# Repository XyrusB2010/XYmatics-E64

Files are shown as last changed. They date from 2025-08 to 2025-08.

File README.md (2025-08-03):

# XYmatics E64
XYmatics E64 (Engine, 64-bit) is a 5-axis Klipper mainboard, powered by a Raspberry Pi CM4 and STM32F407. It was originally built for <a href='https://github.com/XyrusB2010/XYmatics-Alpha/tree/main'>XYmatics Alpha</a>, but you can also use it for most 3D Printers.

## E64 Features
- Powered by STM32F407VET6 (MCU) and Raspberry Pi CM4 (Host)
- 1 USB-micro OTG port + 2 USB-A ports + 1 USB JST breakout, 100 Mbit RJ45 Socket for LAN, Micro SD card for extra storage
- 5 TMC2209 Stepsticks to drive stepper motors
- 3 Endstops/Switches
- 5 Controllable fans on base board + 1 for Raspberry Pi
- 8 CAN FD bus ports to reduce amount of cables
- CSI for camera input
- HDMI or DSI for display output
- I2C bus broken out

## E64 PCB
E64 PCB

# XYmatics X42
XYmatics X42 (Xpansion, for 42mm motors) is a Klipper expansion board, designed to mount onto 42mm stepper motors. Powered by a STM32G0B1, it communicates to the E64 mainboard through CAN FD. This board simplifies the mainboard, and reduces the amount of cables going out. The X42 can also be used with most other 3D Printers.

## X42 Features
- Powered by STM32G0B1CBT6
- Supports Laser engravers, CNC routers and FDM extruders
- TJA1051T CAN FD module to communicate with E64
- ~~BLTouch compatible~~
- Two PWM controllable fans
- ADXL345 accelerometer included
- ~~3~~ 1 Endstop/Switch
- I2C bus ~~and neopixel~~ broken out
>  [!NOTE]
>  May re-add these removed features in future if possible.

## X42 PCB
X42 PCB front view
X42 PCB back view

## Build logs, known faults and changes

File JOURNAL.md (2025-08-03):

---
title: "XYmatics-E64"
author: "Xyrus Babao"
description: "5-axis Klipper-powered mainboard"
created_at: "2025-07-07"
---

### <b>Total time spent: 13 hours 45 minutes</b>

# 7/07/2025 - Begin PCB design
For the PCB design, I am using KiCad with a few components imported from <a href="https://snapeda.com/">SnapEDA.</a> I have named <a href='https://github.com/XyrusB2010/XYmatics-Alpha/tree/main'>XYmatics-Alpha's</a> mainboard E64 (Engine64). It utilises a CM4/CM5 compute module running Klipper firmware to control the main MCU - an STM32F407. Like most Klipper systems, the compute module does not directly control the motors, sensors, etc, and instead outputs commands via USB to the STM32. I have completed desigining the Compute module side, and just need to complete the STM32 and other components. Below is an image of the CM4 schematic.

XYmatics-E64 CM4 schematic

(Excuse the resolution, you can view a PDF of the schematic <a href="https://github.com/XyrusB2010/XYmatics-E64/blob/main/Schematics/xymatics-e64.pdf">here.</a>)

<b>Total time - 45 minutes</b>

# 14/07/2025 - Finish STM32 schematic and begin X42 schematic
Today I have completed the schematic for the STM32F407. It has what most other 3D Printer mainboards have, but also includes 8 CAN FD bus ports for connecting expansion boards (XYmatics-X42). It uses the high-speed TJA1051T for CAN FD communication. 5 TMC2209 Stepsticks are used to drive the main stepper motors. 5 controllable fans are included, as well as another MOSFET for the heatbed. 3 endstops/switches are included to home the printer. The entire system runs on 24V, which is the standard for most 3D printer mainboards.

XYmatics-E64 STM32F407 schematic

<a href="https://github.com/XyrusB2010/XYmatics-E64/blob/main/Schematics/xymatics-e64.pdf">Link to schematic PDF</a>

<b>Total time - 2 hours 15 minutes</b>

# 20/07/2025 - Finish X42 schematic
I have now finished the schematic for the X42. It is quite similar to the BIGTREETECH EBB42 and Mellow Fly SHT-42, but also contains a MOSFET to drive a laser engraver or router motor. Unfortunately, I haven't broken out a USB port yet (although I may fix this in the future). This means the only other way to flash Klipper is through an ST-LINK, or other JTAG/SWD programmer. You can obtain these through Aliexpress for <$2 USD. The X42 also doesn't use a Stepstick driver like the E64 mainboard, but has a directly soldered TMC2209 instead. After looking through the schematics one more time, I should be ready to start designing the PCBs.

XYmatics-E64 X42 schematic

<b>Total time - 2 hours</b>

# 23/07/2025 - Update on X42
The X42 PCB is about 75% completed, I just need to route the components for the CNC router/laser. Due to the limited amount of space on the PCB, some of the components are mounted on the back side (currently just the power supply and regulators). So far the CAN BUS, SWD, Stepper motor, Thermistor, Hotend, Fans, I2C Bus and Buttons have been placed and routed. Unfortunately, I have temporarily removed the Neopixel and BLTouch breakouts due to the lack of space, although I may re-add them later on. Below is an unfinished 3D render of the X42 PCB:

X42 PCB front view
X42 PCB back view

<b>Total time - 1 hour 45 minutes</b>

# 25/07/2025 - Finish X42 PCB
I have now finished designing the PCB for the X42. All GPIOs/breakouts are on the front side, while the power supply and ADXL345 are mounted on the back. Endstops have also been removed due to the small amount of remaining space. This will be added in the first revision. I will begin to route the Raspberry Pi components on the E64, starting with the power supply. Below is a completed 3D render of the X42 PCB:

X42 PCB front view
X42 PCB back view

<b>Total time - 2 hours</b>

# 31/07/2025 - E64 PCB complete
6 days later, the E64 PCB has been finished. Please note that the RPI-GPIO isn't fully broken out, only +5V, +3.3V and I2C Bus have been. Notice how the RPI electronics are on one side while the F407 is on the other, this is to reduce complications with the design. 3 M3 mounting holes have been placed in the corners. The rough dimensions of the board are 192x98mm. The next step is to write the firmware for Klipper, which shouldn't be too hard. Here is a 3D render of the E64 PCB:

E64 PCB front view

<b>Total time - 3 hours</b>

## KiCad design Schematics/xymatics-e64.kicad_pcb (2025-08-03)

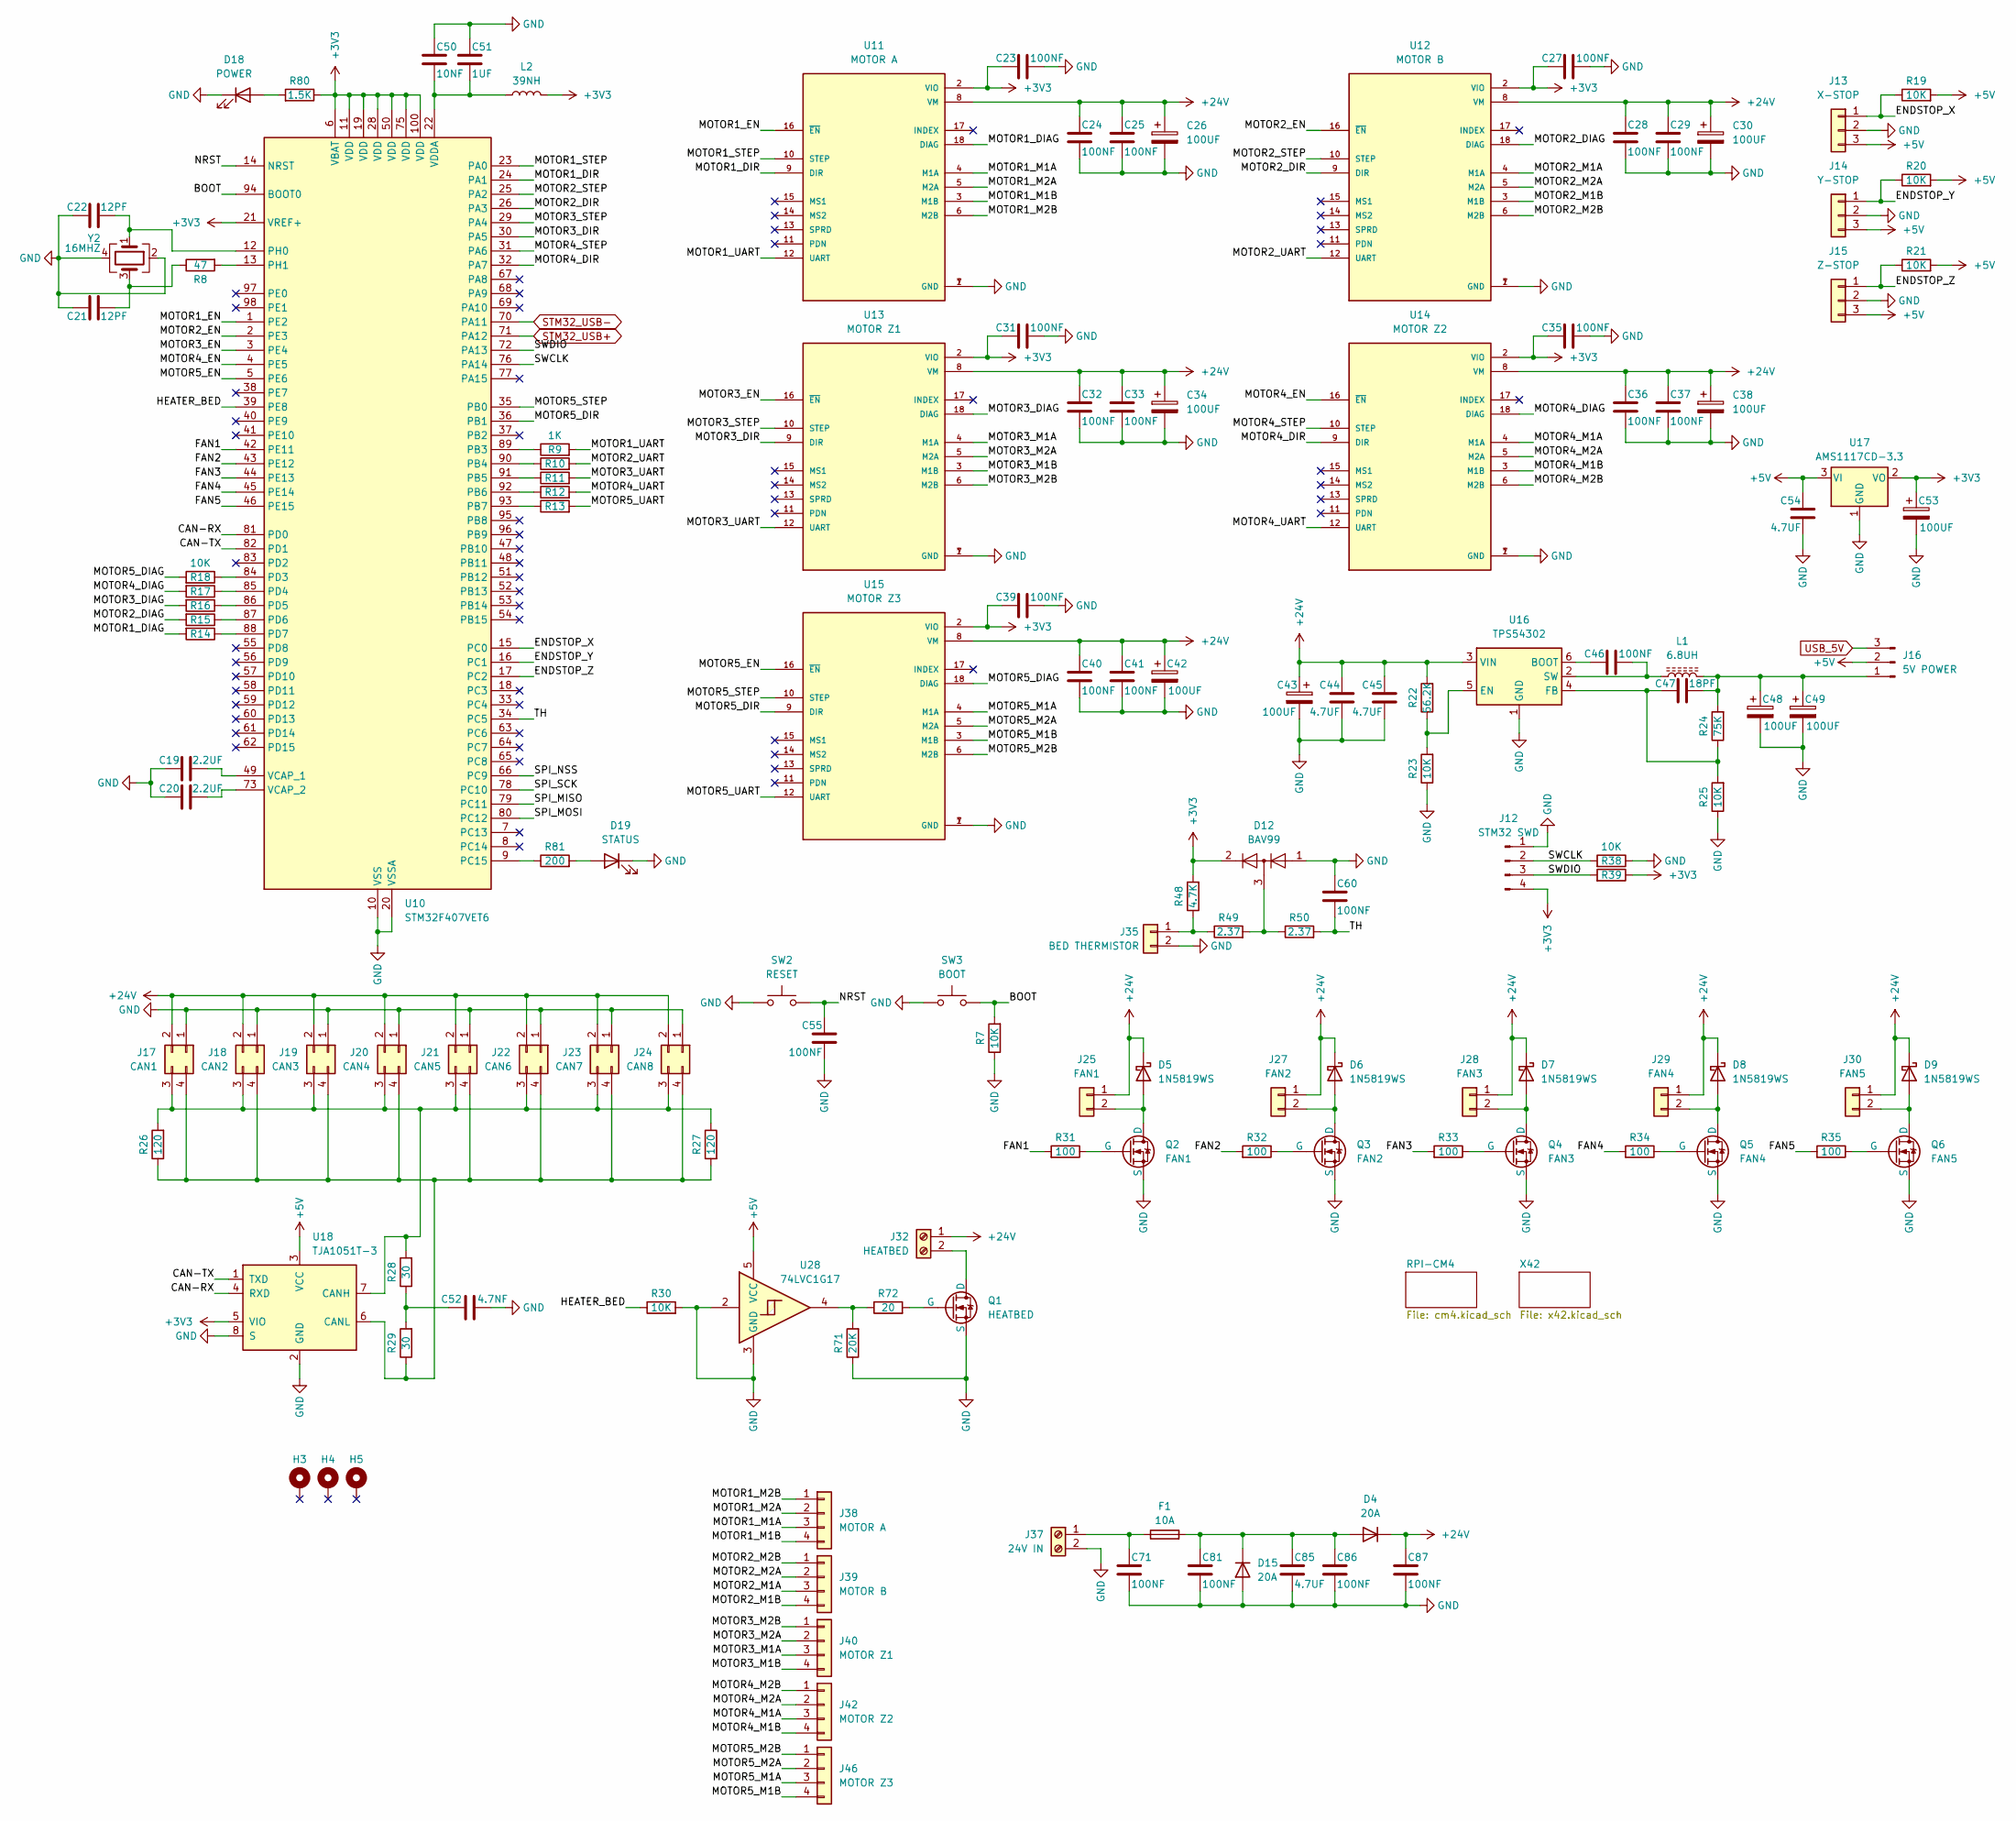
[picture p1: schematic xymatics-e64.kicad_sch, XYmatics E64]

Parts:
C19, C20: 2.2UF; C_0805_2012Metric
C21, C22: 12PF; C_0805_2012Metric
C23, C24, C25, C27, C28, C29, C31, C32, C33, C35, C36, C37, C39, C40, C41, C46, C55, C60, C71, C81, C86, C87: 100NF; C_0805_2012Metric
C26, C30, C34, C38, C42, C43, C48, C49, C53: 100UF; CP_Elec_5x3
C44, C45, C54, C85: 4.7UF; C_0805_2012Metric
C47: 18PF; C_0805_2012Metric
C50: 10NF; C_0805_2012Metric
C51: 1UF; C_0805_2012Metric
C52: 4.7NF; C_0805_2012Metric
D4, D15: 20A; D_SMB
D5, D6, D7, D8, D9: 1N5819WS; D_SOD-323
D12: BAV99; SOT-23
D18: POWER; LED_0805_2012Metric
D19: STATUS; LED_0805_2012Metric
F1: 10A; Fuse_Blade_ATO_directSolder
H3, H4, H5: MountingHole_Pad; MountingHole_3mm_Pad
J12: STM32 SWD; PinHeader_1x04_P2.54mm_Vertical
J13: X-STOP; JST_XH_B3B-XH-A_1x03_P2.50mm_Vertical
J14: Y-STOP; JST_XH_B3B-XH-A_1x03_P2.50mm_Vertical
J15: Z-STOP; JST_XH_B3B-XH-A_1x03_P2.50mm_Vertical
J16: 5V POWER; PinHeader_1x03_P2.54mm_Vertical
J17: CAN1; Molex_Micro-Fit_3.0_43045-0412_2x02_P3.00mm_Vertical
J18: CAN2; Molex_Micro-Fit_3.0_43045-0412_2x02_P3.00mm_Vertical
J19: CAN3; Molex_Micro-Fit_3.0_43045-0412_2x02_P3.00mm_Vertical
J20: CAN4; Molex_Micro-Fit_3.0_43045-0412_2x02_P3.00mm_Vertical
J21: CAN5; Molex_Micro-Fit_3.0_43045-0412_2x02_P3.00mm_Vertical
J22: CAN6; Molex_Micro-Fit_3.0_43045-0412_2x02_P3.00mm_Vertical
J23: CAN7; Molex_Micro-Fit_3.0_43045-0412_2x02_P3.00mm_Vertical
J24: CAN8; Molex_Micro-Fit_3.0_43045-0412_2x02_P3.00mm_Vertical
J25: FAN1; JST_XH_B2B-XH-A_1x02_P2.50mm_Vertical
J27: FAN2; JST_XH_B2B-XH-A_1x02_P2.50mm_Vertical
J28: FAN3; JST_XH_B2B-XH-A_1x02_P2.50mm_Vertical
J29: FAN4; JST_XH_B2B-XH-A_1x02_P2.50mm_Vertical
J30: FAN5; JST_XH_B2B-XH-A_1x02_P2.50mm_Vertical
J32: HEATBED; TerminalBlock_MaiXu_MX126-5.0-02P_1x02_P5.00mm
J35: BED THERMISTOR; JST_XH_B2B-XH-A_1x02_P2.50mm_Vertical
J37: 24V IN; TerminalBlock_MaiXu_MX126-5.0-02P_1x02_P5.00mm
J38: MOTOR A; JST_XH_B4B-XH-A_1x04_P2.50mm_Vertical
J39: MOTOR B; JST_XH_B4B-XH-A_1x04_P2.50mm_Vertical
J40: MOTOR Z1; JST_XH_B4B-XH-A_1x04_P2.50mm_Vertical
J42: MOTOR Z2; JST_XH_B4B-XH-A_1x04_P2.50mm_Vertical
J46: MOTOR Z3; JST_XH_B4B-XH-A_1x04_P2.50mm_Vertical
L1: 6.8UH; L_6.3x6.3_H3
L2: 39NH; L_0805_2012Metric
Q1: HEATBED; TO-252-2
Q2: FAN1; SOT-23
Q3: FAN2; SOT-23
Q4: FAN3; SOT-23
Q5: FAN4; SOT-23
Q6: FAN5; SOT-23
R7, R14, R15, R16, R17, R18, R19, R20, R21, R23, R25, R30, R38, R39: 10K; R_0805_2012Metric
R8: 47; R_0805_2012Metric
R9, R10, R11, R12, R13: 1K; R_0805_2012Metric
R22: 56.2K; R_1206_3216Metric
R24: 75K; R_1206_3216Metric
R26, R27: 120; R_0805_2012Metric
R28, R29: 30; R_0805_2012Metric
R31, R32, R33, R34, R35: 100; R_0805_2012Metric
R48: 4.7K; R_0805_2012Metric
R49, R50: 2.37; R_0805_2012Metric
R71: 20K; R_0805_2012Metric
R72: 20; R_0805_2012Metric
R80: 1.5K; R_0805_2012Metric
R81: 200; R_0805_2012Metric
SW2: RESET; SW_Tactile_SPST_NO_Straight_CK_PTS636Sx25SMTRLFS
SW3: BOOT; SW_Tactile_SPST_NO_Straight_CK_PTS636Sx25SMTRLFS
U10: STM32F407VET6; LQFP-100_14x14mm_P0.5mm
U11: MOTOR A; MODULE_TMC2209_SILENTSTEPSTICK; PARTREV 1.20
U12: MOTOR B; MODULE_TMC2209_SILENTSTEPSTICK; PARTREV 1.20
U13: MOTOR Z1; MODULE_TMC2209_SILENTSTEPSTICK; PARTREV 1.20
U14: MOTOR Z2; MODULE_TMC2209_SILENTSTEPSTICK; PARTREV 1.20
U15: MOTOR Z3; MODULE_TMC2209_SILENTSTEPSTICK; PARTREV 1.20
U16: TPS54302; SOT-23-6
U17: AMS1117CD-3.3; TO-252-2
U18: TJA1051T-3; SOIC-8_3.9x4.9mm_P1.27mm
U28: 74LVC1G17; SOT-23-5
Y2: 16MHZ; Crystal_SMD_Abracon_ABM3B-4Pin_5.0x3.2mm

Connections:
+3V3: C23.2, C27.2, C31.2, C35.2, C39.2, C53.1, D12.2 (A), J12.4, L2.2, R39.1, R48.2, R80.1, U10.6 (VBAT), U10.11 (VDD), U10.19 (VDD), U10.21 (VREF+), U10.28 (VDD), U10.50 (VDD), U10.75 (VDD), U10.100 (VDD), U11.2 (VIO), U12.2 (VIO), U13.2 (VIO), U14.2 (VIO), U15.2 (VIO), U17.2 (VO), U18.5 (VIO)
+5V: C54.1, J13.3, J14.3, J15.3, J16.2, R19.2, R20.2, R21.2, U17.3 (VI), U18.3 (VCC), U28.5 (VCC); also elsewhere on the board
+24V: C24.1, C25.1, C26.1, C28.1, C29.1, C30.1, C32.1, C33.1, C34.1, C36.1, C37.1, C38.1, C40.1, C41.1, C42.1, C43.1, C44.1, C45.1, C87.1, D4.1 (K), D5.1 (K), D6.1 (K), D7.1 (K), D8.1 (K), D9.1 (K), J17.2, J18.2, J19.2, J20.2, J21.2, J22.2, J23.2, J24.2, J25.1, J27.1, J28.1, J29.1, J30.1, J32.1, R22.2, U11.8 (VM), U12.8 (VM), U13.8 (VM), U14.8 (VM), U15.8 (VM), U16.3 (VIN)
/BOOT: R7.2, SW3.2, U10.94 (BOOT0)
/CAN-RX: U10.81 (PD0), U18.4 (RXD)
/CAN-TX: U10.82 (PD1), U18.1 (TXD)
/ENDSTOP_X: J13.1, R19.1, U10.15 (PC0)
/ENDSTOP_Y: J14.1, R20.1, U10.16 (PC1)
/ENDSTOP_Z: J15.1, R21.1, U10.17 (PC2)
/FAN1: R31.2, U10.42 (PE11)
/FAN2: R32.2, U10.43 (PE12)
/FAN3: R33.2, U10.44 (PE13)
/FAN4: R34.2, U10.45 (PE14)
/FAN5: R35.2, U10.46 (PE15)
/HEATER_BED: R30.1, U10.39 (PE8)
/MOTOR1_DIAG: R14.2, U11.18 (DIAG)
/MOTOR1_DIR: U10.24 (PA1), U11.9 (DIR)
/MOTOR1_EN: U10.1 (PE2), U11.16 (~EN)
/MOTOR1_M1A: J38.3, U11.4 (M1A)
/MOTOR1_M1B: J38.4, U11.3 (M1B)
/MOTOR1_M2A: J38.2, U11.5 (M2A)
/MOTOR1_M2B: J38.1, U11.6 (M2B)
/MOTOR1_STEP: U10.23 (PA0), U11.10 (STEP)
/MOTOR1_UART: R9.2, U11.12 (UART)
/MOTOR2_DIAG: R15.2, U12.18 (DIAG)
/MOTOR2_DIR: U10.26 (PA3), U12.9 (DIR)
/MOTOR2_EN: U10.2 (PE3), U12.16 (~EN)
/MOTOR2_M1A: J39.3, U12.4 (M1A)
/MOTOR2_M1B: J39.4, U12.3 (M1B)
/MOTOR2_M2A: J39.2, U12.5 (M2A)
/MOTOR2_M2B: J39.1, U12.6 (M2B)
/MOTOR2_STEP: U10.25 (PA2), U12.10 (STEP)
/MOTOR2_UART: R10.2, U12.12 (UART)
/MOTOR3_DIAG: R16.2, U13.18 (DIAG)
/MOTOR3_DIR: U10.30 (PA5), U13.9 (DIR)
/MOTOR3_EN: U10.3 (PE4), U13.16 (~EN)
/MOTOR3_M1A: J40.3, U13.4 (M1A)
/MOTOR3_M1B: J40.4, U13.3 (M1B)
/MOTOR3_M2A: J40.2, U13.5 (M2A)
/MOTOR3_M2B: J40.1, U13.6 (M2B)
/MOTOR3_STEP: U10.29 (PA4), U13.10 (STEP)
/MOTOR3_UART: R11.2, U13.12 (UART)
/MOTOR4_DIAG: R17.2, U14.18 (DIAG)
/MOTOR4_DIR: U10.32 (PA7), U14.9 (DIR)
/MOTOR4_EN: U10.4 (PE5), U14.16 (~EN)
/MOTOR4_M1A: J42.3, U14.4 (M1A)
/MOTOR4_M1B: J42.4, U14.3 (M1B)
/MOTOR4_M2A: J42.2, U14.5 (M2A)
/MOTOR4_M2B: J42.1, U14.6 (M2B)
/MOTOR4_STEP: U10.31 (PA6), U14.10 (STEP)
/MOTOR4_UART: R12.2, U14.12 (UART)
/MOTOR5_DIAG: R18.2, U15.18 (DIAG)
/MOTOR5_DIR: U10.36 (PB1), U15.9 (DIR)
/MOTOR5_EN: U10.5 (PE6), U15.16 (~EN)
/MOTOR5_M1A: J46.3, U15.4 (M1A)
/MOTOR5_M1B: J46.4, U15.3 (M1B)
/MOTOR5_M2A: J46.2, U15.5 (M2A)
/MOTOR5_M2B: J46.1, U15.6 (M2B)
/MOTOR5_STEP: U10.35 (PB0), U15.10 (STEP)
/MOTOR5_UART: R13.2, U15.12 (UART)
/NRST: C55.1, SW2.2, U10.14 (NRST)
/SPI_MISO: U10.79 (PC11)
/SPI_MOSI: U10.80 (PC12)
/SPI_NSS: U10.66 (PC9)
/SPI_SCK: U10.78 (PC10)
/SWCLK: J12.2, R38.2, U10.76 (PA14)
/SWDIO: J12.3, R39.2, U10.72 (PA13)
/TH: C60.2, R50.2, U10.34 (PC5)
GND: C19.2, C20.2, C21.1, C22.1, C23.1, C24.2, C25.2, C26.2, C27.1, C28.2, C29.2, C30.2, C31.1, C32.2, C33.2, C34.2, C35.1, C36.2, C37.2, C38.2, C39.1, C40.2, C41.2, C42.2, C43.2, C44.2, C45.2, C48.2, C49.2, C50.1, C51.1, C52.2, C53.2, C54.2, C55.2, C60.1, C71.2, C81.2, C85.2, C86.2, C87.2, D12.1 (K), D15.2 (A), D18.1 (K), D19.1 (K), J12.1, J13.2, J14.2, J15.2, J17.1, J18.1, J19.1, J20.1, J21.1, J22.1, J23.1, J24.1, J35.2, J37.2, Q1.3 (S), Q2.3 (S), Q3.3 (S), Q4.3 (S), Q5.3 (S), Q6.3 (S), R7.1, R23.1, R25.1, R30.2, R38.1, R71.1, SW2.1, SW3.1, U10.10 (VSS), U10.20 (VSSA), U10.27 (VSS), U10.74 (VSS), U10.99 (VSS), U11.1 (GND), U11.7 (GND), U12.1 (GND), U12.7 (GND), U13.1 (GND), U13.7 (GND), U14.1 (GND), U14.7 (GND), U15.1 (GND), U15.7 (GND), U16.1 (GND), U17.1 (GND), U18.2 (GND), U18.8 (S), U28.2, U28.3 (GND), Y2.2, Y2.4; also elsewhere on the board
unnamed: C21.2, R8.1, Y2.3
unnamed: C52.1, R28.1, R29.2
unnamed: D5.2 (A), J25.2, Q2.1 (D)
unnamed: D6.2 (A), J27.2, Q3.1 (D)
unnamed: D7.2 (A), J28.2, Q4.1 (D)
unnamed: D8.2 (A), J29.2, Q5.1 (D)
unnamed: D9.2 (A), J30.2, Q6.1 (D)
unnamed: D12.3 (K), R49.2, R50.1
unnamed: C81.1, C85.1, C86.1, D4.2 (A), D15.1 (K), F1.2
unnamed: D18.2 (A), R80.2
unnamed: D19.2 (A), R81.2
unnamed: C47.1, C48.1, C49.1, J16.1, L1.2, R24.2
unnamed: J17.3, J18.3, J19.3, J20.3, J21.3, J22.3, J23.3, J24.3, R26.2, R27.1, R28.2, U18.7 (CANH)
unnamed: J17.4, J18.4, J19.4, J20.4, J21.4, J22.4, J23.4, J24.4, R26.1, R27.2, R29.1, U18.6 (CANL)
unnamed: J32.2, Q1.2 (D)
unnamed: J35.1, R48.1, R49.1
unnamed: C71.1, F1.1, J37.1
unnamed: Q1.1 (G), R72.2
unnamed: Q2.2 (G), R31.1
unnamed: Q3.2 (G), R32.1
unnamed: Q4.2 (G), R33.1
unnamed: Q5.2 (G), R34.1
unnamed: Q6.2 (G), R35.1
unnamed: R71.2, R72.1, U28.4
unnamed: R9.1, U10.89 (PB3)
unnamed: R10.1, U10.90 (PB4)
unnamed: R11.1, U10.91 (PB5)
unnamed: R12.1, U10.92 (PB6)
unnamed: R13.1, U10.93 (PB7)
unnamed: R81.1, U10.9 (PC15)
unnamed: R18.1, U10.84 (PD3)
unnamed: R17.1, U10.85 (PD4)
unnamed: R16.1, U10.86 (PD5)
unnamed: R15.1, U10.87 (PD6)
unnamed: R14.1, U10.88 (PD7)
unnamed: C22.2, U10.12 (PH0), Y2.1
unnamed: R8.2, U10.13 (PH1)
unnamed: C19.1, U10.49 (VCAP_1)
unnamed: C20.1, U10.73 (VCAP_2)
unnamed: C50.2, C51.2, L2.1, U10.22 (VDDA)
unnamed: C46.2, U16.6 (BOOT)
unnamed: R22.1, R23.2, U16.5 (EN)
unnamed: C47.2, R24.1, R25.2, U16.4 (FB)
unnamed: C46.1, L1.1, U16.2 (SW)
STM32_USB+: U10.71 (PA12); also elsewhere on the board
STM32_USB-: U10.70 (PA11); also elsewhere on the board
USB_5V: J16.3; also elsewhere on the board

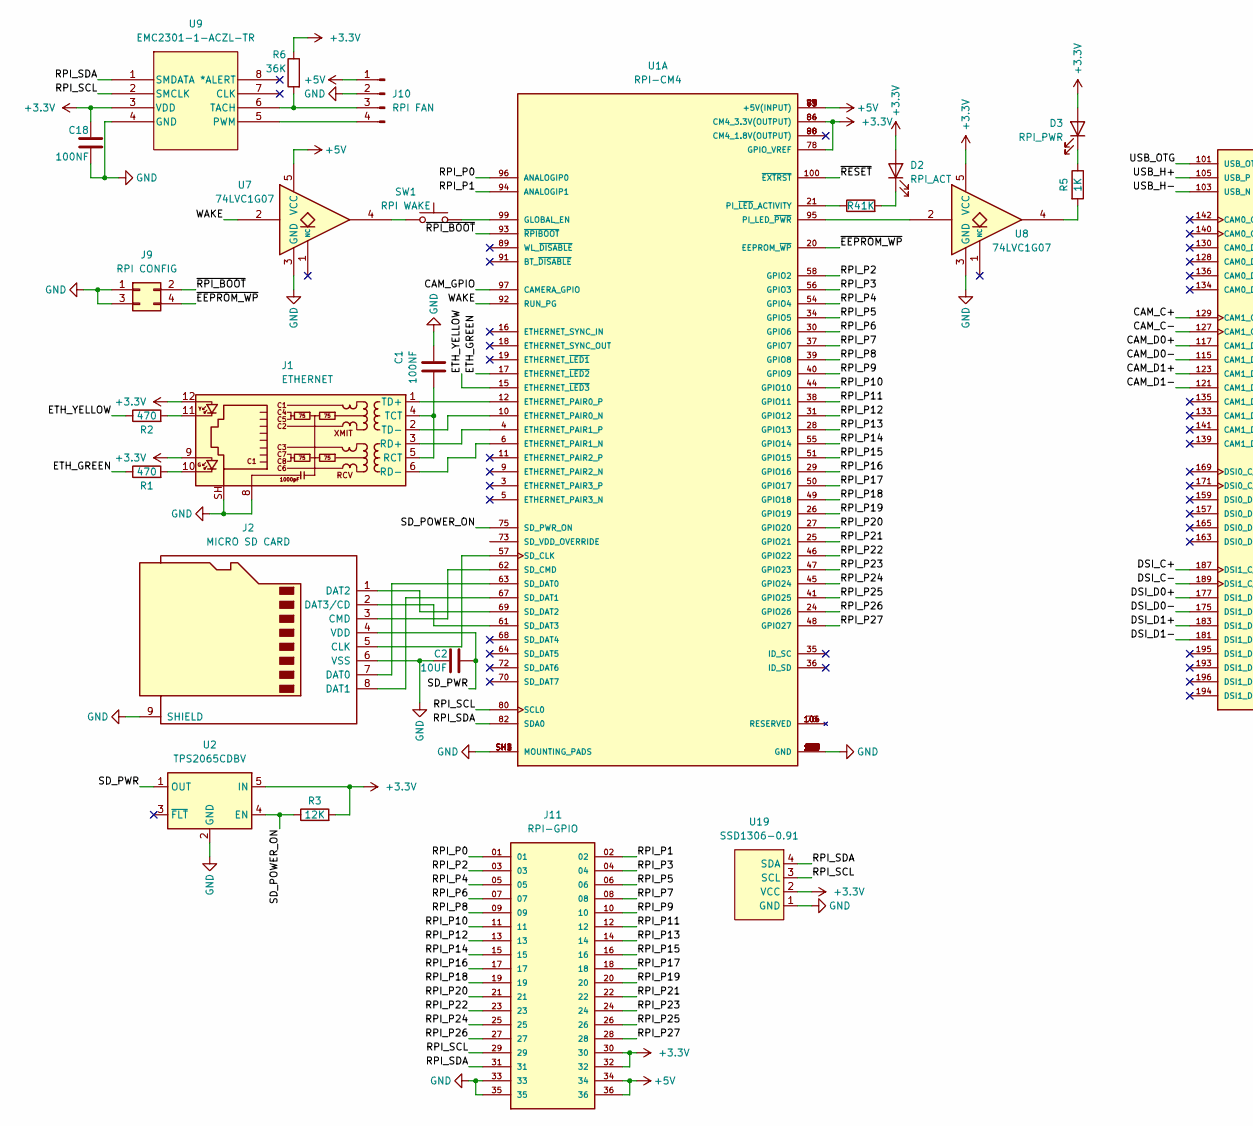
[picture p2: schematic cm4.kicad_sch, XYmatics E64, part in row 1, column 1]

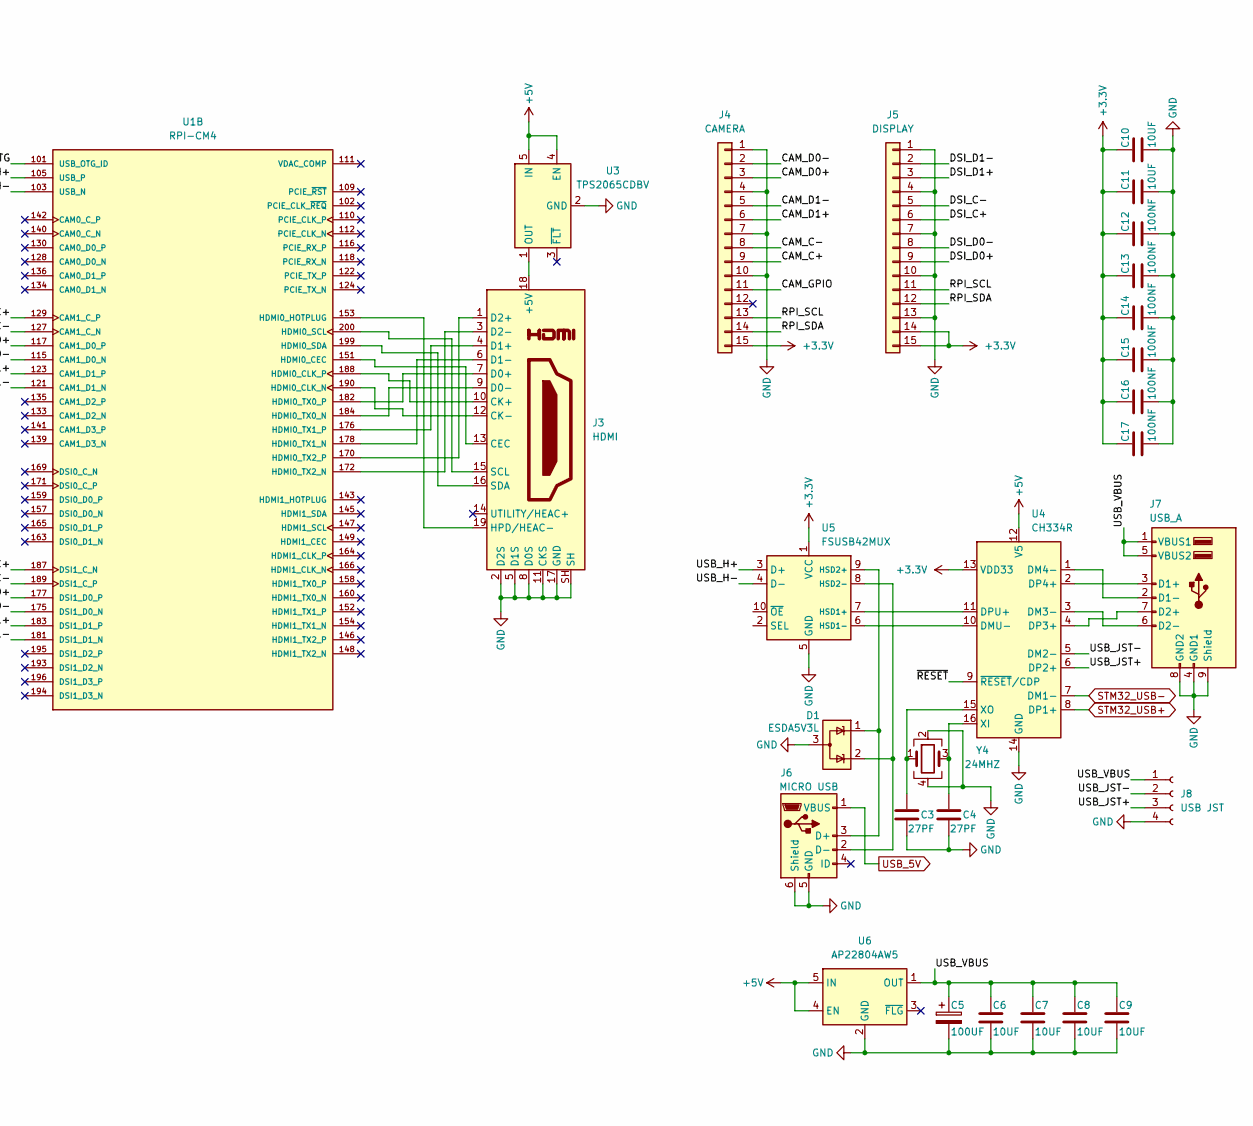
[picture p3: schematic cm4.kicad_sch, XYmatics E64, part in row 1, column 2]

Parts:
C1, C12, C13, C14, C15, C16, C17, C18: 100NF; C_0805_2012Metric
C2, C6, C7, C8, C9, C10, C11: 10UF; C_0805_2012Metric
C3, C4: 27PF; C_0805_2012Metric
C5: 100UF; CP_Elec_5x3
D1: ESDA5V3L; SOT-23-3
D2: RPI_ACT; LED_0805_2012Metric
D3: RPI_PWR; LED_0805_2012Metric
J1: ETHERNET; RJ45_Hanrun_HR911105A_Horizontal
J2: MICRO SD CARD; microSD_HC_Wuerth_693072010801
J3: HDMI; HDMI_A_Molex_208658-1001_Horizontal
J4: CAMERA; Molex_502231-1500_1x15-1SH_P0.5mm_Vertical
J5: DISPLAY; Molex_502231-1500_1x15-1SH_P0.5mm_Vertical
J6: MICRO USB; USB_Micro-B_Molex_47346-0001
J7: USB_A; USB_A_CUI_UJ2-ADH-TH_Horizontal_Stacked
J8: USB JST; JST_XH_B4B-XH-A_1x04_P2.50mm_Vertical
J9: RPI CONFIG; PinHeader_2x02_P2.54mm_Vertical
J10: RPI FAN; PinHeader_1x04_P2.54mm_Vertical
J11: RPI-GPIO; SAMTEC_TST-118-01-T-D; PARTREV R
R1, R2: 470; R_0805_2012Metric
R3: 12K; R_0805_2012Metric
R4, R5: 1K; R_0805_2012Metric
R6: 36K; R_0805_2012Metric
SW1: RPI WAKE; SW_Tactile_SPST_NO_Straight_CK_PTS636Sx25SMTRLFS
U1: RPI-CM4; MODULE_CM4102008; PARTREV 2021-10-12
U2, U3: TPS2065CDBV; SOT-23-5
U4: CH334R; QSOP-16_3.9x4.9mm_P0.635mm
U5: FSUSB42MUX; MSOP-10_3x3mm_P0.5mm
U6: AP22804AW5; SOT-23-5
U7, U8: 74LVC1G07; SOT-23-5
U9: EMC2301-1-ACZL-TR; MSOP8_MC_MCH
U19: SSD1306-0.91; OLED-12832
Y4: 24MHZ; Crystal_SMD_Abracon_ABM3B-4Pin_5.0x3.2mm

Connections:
+3.3V: C10.1, C11.1, C12.1, C13.1, C14.1, C15.1, C16.1, C17.1, C18.1, D2.2 (A), D3.2 (A), J1.9, J1.12, J4.15, J5.14, J5.15, J11.30, J11.32, R3.2, R6.1, U1.78 (GPIO_VREF), U1.84 (CM4_3.3V(OUTPUT)), U1.86 (CM4_3.3V(OUTPUT)), U2.5 (IN), U4.13 (VDD33), U5.1 (VCC), U8.5 (VCC), U9.3 (VDD), U19.2 (VCC)
+5V: J10.1, J11.34, J11.36, U1.77 (+5V(INPUT)), U1.79 (+5V(INPUT)), U1.81 (+5V(INPUT)), U1.83 (+5V(INPUT)), U1.85 (+5V(INPUT)), U1.87 (+5V(INPUT)), U3.4 (EN), U3.5 (IN), U4.12 (V5), U6.4 (EN), U6.5 (IN), U7.5 (VCC); also elsewhere on the board
/RPI-CM4/CAM_C+: J4.9, U1.129 (CAM1_C_P)
/RPI-CM4/CAM_C-: J4.8, U1.127 (CAM1_C_N)
/RPI-CM4/CAM_D0+: J4.3, U1.117 (CAM1_D0_P)
/RPI-CM4/CAM_D0-: J4.2, U1.115 (CAM1_D0_N)
/RPI-CM4/CAM_D1+: J4.6, U1.123 (CAM1_D1_P)
/RPI-CM4/CAM_D1-: J4.5, U1.121 (CAM1_D1_N)
/RPI-CM4/CAM_GPIO: J4.11, U1.97 (CAMERA_GPIO)
/RPI-CM4/DSI_C+: J5.6, U1.187 (DSI1_C_N)
/RPI-CM4/DSI_C-: J5.5, U1.189 (DSI1_C_P)
/RPI-CM4/DSI_D0+: J5.9, U1.177 (DSI1_D0_P)
/RPI-CM4/DSI_D0-: J5.8, U1.175 (DSI1_D0_N)
/RPI-CM4/DSI_D1+: J5.3, U1.183 (DSI1_D1_P)
/RPI-CM4/DSI_D1-: J5.2, U1.181 (DSI1_D1_N)
/RPI-CM4/ETH_GREEN: R1.1, U1.17 (ETHERNET_~LED2)
/RPI-CM4/ETH_YELLOW: R2.1, U1.15 (ETHERNET_~LED3)
/RPI-CM4/RPI_P0: J11.01, U1.96 (ANALOGIP0)
/RPI-CM4/RPI_P1: J11.02, U1.94 (ANALOGIP1)
/RPI-CM4/RPI_P2: J11.03, U1.58 (GPIO2)
/RPI-CM4/RPI_P3: J11.04, U1.56 (GPIO3)
/RPI-CM4/RPI_P4: J11.05, U1.54 (GPIO4)
/RPI-CM4/RPI_P5: J11.06, U1.34 (GPIO5)
/RPI-CM4/RPI_P6: J11.07, U1.30 (GPIO6)
/RPI-CM4/RPI_P7: J11.08, U1.37 (GPIO7)
/RPI-CM4/RPI_P8: J11.09, U1.39 (GPIO8)
/RPI-CM4/RPI_P9: J11.10, U1.40 (GPIO9)
/RPI-CM4/RPI_P10: J11.11, U1.44 (GPIO10)
/RPI-CM4/RPI_P11: J11.12, U1.38 (GPIO11)
/RPI-CM4/RPI_P12: J11.13, U1.31 (GPIO12)
/RPI-CM4/RPI_P13: J11.14, U1.28 (GPIO13)
/RPI-CM4/RPI_P14: J11.15, U1.55 (GPIO14)
/RPI-CM4/RPI_P15: J11.16, U1.51 (GPIO15)
/RPI-CM4/RPI_P16: J11.17, U1.29 (GPIO16)
/RPI-CM4/RPI_P17: J11.18, U1.50 (GPIO17)
/RPI-CM4/RPI_P18: J11.19, U1.49 (GPIO18)
/RPI-CM4/RPI_P19: J11.20, U1.26 (GPIO19)
/RPI-CM4/RPI_P20: J11.21, U1.27 (GPIO20)
/RPI-CM4/RPI_P21: J11.22, U1.25 (GPIO21)
/RPI-CM4/RPI_P22: J11.23, U1.46 (GPIO22)
/RPI-CM4/RPI_P23: J11.24, U1.47 (GPIO23)
/RPI-CM4/RPI_P24: J11.25, U1.45 (GPIO24)
/RPI-CM4/RPI_P25: J11.26, U1.41 (GPIO25)
/RPI-CM4/RPI_P26: J11.27, U1.24 (GPIO26)
/RPI-CM4/RPI_P27: J11.28, U1.48 (GPIO27)
/RPI-CM4/RPI_SCL: J4.13, J5.11, J11.29, U1.80 (SCL0), U9.2 (SMCLK), U19.3 (SCL)
/RPI-CM4/RPI_SDA: J4.14, J5.12, J11.31, U1.82 (SDA0), U9.1 (SMDATA), U19.4 (SDA)
/RPI-CM4/SD_POWER_ON: R3.1, U1.75 (SD_PWR_ON), U2.4 (EN)
/RPI-CM4/SD_PWR: C2.1, J2.4 (VDD), U2.1 (OUT)
/RPI-CM4/USB_H+: U1.105 (USB_P), U5.3 (D+)
/RPI-CM4/USB_H-: U1.103 (USB_N), U5.4 (D-)
/RPI-CM4/USB_JST+: J8.3, U4.6 (DP2+)
/RPI-CM4/USB_JST-: J8.2, U4.5 (DM2-)
/RPI-CM4/USB_OTG: U1.101 (USB_OTG_ID)
/RPI-CM4/USB_VBUS: C5.1, C6.1, C7.1, C8.1, C9.1, J7.1 (VBUS1), J7.5 (VBUS2), J8.1, U6.1 (OUT)
/RPI-CM4/WAKE: U1.92 (RUN_PG), U7.2
/RPI-CM4/~EEPROM_WP: J9.4, U1.20 (EEPROM_~WP)
/RPI-CM4/~RESET: U1.100 (~EXTRST), U4.9 (~RESET/CDP)
/RPI-CM4/~RPI_BOOT: J9.2, U1.93 (~RPIBOOT)
GND: C1.1, C2.2, C3.2, C4.2, C5.2, C6.2, C7.2, C8.2, C9.2, C10.2, C11.2, C12.2, C13.2, C14.2, C15.2, C16.2, C17.2, C18.2, D1.3 (A), J1.8, J1.SH, J2.6 (VSS), J2.9 (SHIELD), J3.2 (D2S), J3.5 (D1S), J3.8 (D0S), J3.11 (CKS), J3.17 (GND), J3.SH, J4.1, J4.4, J4.7, J4.10, J5.1, J5.4, J5.7, J5.10, J5.13, J6.5 (GND), J6.6 (Shield), J7.4 (GND1), J7.8 (GND2), J7.9 (Shield), J8.4, J9.1, J9.3, J10.2, J11.33, J11.35, U1.1 (GND), U1.2 (GND), U1.7 (GND), U1.8 (GND), U1.13 (GND), U1.14 (GND), U1.22 (GND), U1.23 (GND), U1.32 (GND), U1.33 (GND), U1.42 (GND), U1.43 (GND), U1.52 (GND), U1.53 (GND), U1.59 (GND), U1.60 (GND), U1.65 (GND), U1.66 (GND), U1.71 (GND), U1.74 (GND), U1.98 (GND), U1.107 (GND), U1.108 (GND), U1.113 (GND), U1.114 (GND), U1.119 (GND), U1.120 (GND), U1.125 (GND), U1.126 (GND), U1.131 (GND), U1.132 (GND), U1.137 (GND), U1.138 (GND), U1.144 (GND), U1.150 (GND), U1.155 (GND), U1.156 (GND), U1.161 (GND), U1.162 (GND), U1.167 (GND), U1.168 (GND), U1.173 (GND), U1.174 (GND), U1.179 (GND), U1.180 (GND), U1.185 (GND), U1.186 (GND), U1.191 (GND), U1.192 (GND), U1.197 (GND), U1.198 (GND), U1.SH1 (MOUNTING_PADS), U1.SH2 (MOUNTING_PADS), U1.SH3 (MOUNTING_PADS), U1.SH4 (MOUNTING_PADS), U2.2 (GND), U3.2 (GND), U4.14 (GND), U5.5 (GND), U6.2 (GND), U7.3 (GND), U8.3 (GND), U9.4 (GND), U19.1 (GND), Y4.2, Y4.4; also elsewhere on the board
unnamed: D2.1 (K), R4.2
unnamed: D3.1 (K), R5.1
unnamed: J1.10, R1.2
unnamed: J1.11, R2.2
unnamed: C1.2, J1.4 (TCT), J1.5 (RCT)
unnamed: J1.3 (RD+), U1.4 (ETHERNET_PAIR1_P)
unnamed: J1.6 (RD-), U1.6 (ETHERNET_PAIR1_N)
unnamed: J1.1 (TD+), U1.12 (ETHERNET_PAIR0_P)
unnamed: J1.2 (TD-), U1.10 (ETHERNET_PAIR0_N)
unnamed: J2.5 (CLK), U1.57 (SD_CLK)
unnamed: J2.3 (CMD), U1.62 (SD_CMD)
unnamed: J2.7 (DAT0), U1.63 (SD_DAT0)
unnamed: J2.8 (DAT1), U1.67 (SD_DAT1)
unnamed: J2.1 (DAT2), U1.69 (SD_DAT2)
unnamed: J2.2 (DAT3/CD), U1.61 (SD_DAT3)
unnamed: J3.18 (+5V), U3.1 (OUT)
unnamed: J3.13 (CEC), U1.151 (HDMI0_CEC)
unnamed: J3.10 (CK+), U1.188 (HDMI0_CLK_P)
unnamed: J3.12 (CK-), U1.190 (HDMI0_CLK_N)
unnamed: J3.7 (D0+), U1.182 (HDMI0_TX0_P)
unnamed: J3.9 (D0-), U1.184 (HDMI0_TX0_N)
unnamed: J3.4 (D1+), U1.176 (HDMI0_TX1_P)
unnamed: J3.6 (D1-), U1.178 (HDMI0_TX1_N)
unnamed: J3.1 (D2+), U1.170 (HDMI0_TX2_P)
unnamed: J3.3 (D2-), U1.172 (HDMI0_TX2_N)
unnamed: J3.19 (HPD/HEAC-), U1.153 (HDMI0_HOTPLUG)
unnamed: J3.15 (SCL), U1.200 (HDMI0_SCL)
unnamed: J3.16 (SDA), U1.199 (HDMI0_SDA)
unnamed: D1.1 (K), J6.3 (D+), U5.9 (HSD2+)
unnamed: D1.2 (K), J6.2 (D-), U5.8 (HSD2-)
unnamed: J7.3 (D1+), U4.2 (DP4+)
unnamed: J7.2 (D1-), U4.1 (DM4-)
unnamed: J7.7 (D2+), U4.4 (DP3+)
unnamed: J7.6 (D2-), U4.3 (DM3-)
unnamed: J10.3, R6.2, U9.6 (TACH)
unnamed: J10.4, U9.5 (PWM)
unnamed: R5.2, U8.4
unnamed: SW1.2, U7.4
unnamed: SW1.1, U1.99 (GLOBAL_EN)
unnamed: U1.95 (PI_LED_~PWR), U8.2
unnamed: R4.1, U1.21 (PI_~LED_ACTIVITY)
unnamed: U4.10 (DMU-), U5.6 (HSD1-)
unnamed: U4.11 (DPU+), U5.7 (HSD1+)
unnamed: C4.1, U4.16 (XI), Y4.3
unnamed: C3.1, U4.15 (XO), Y4.1
STM32_USB+: U4.8 (DP1+); also elsewhere on the board
STM32_USB-: U4.7 (DM1-); also elsewhere on the board
USB_5V: J6.1 (VBUS); also elsewhere on the board

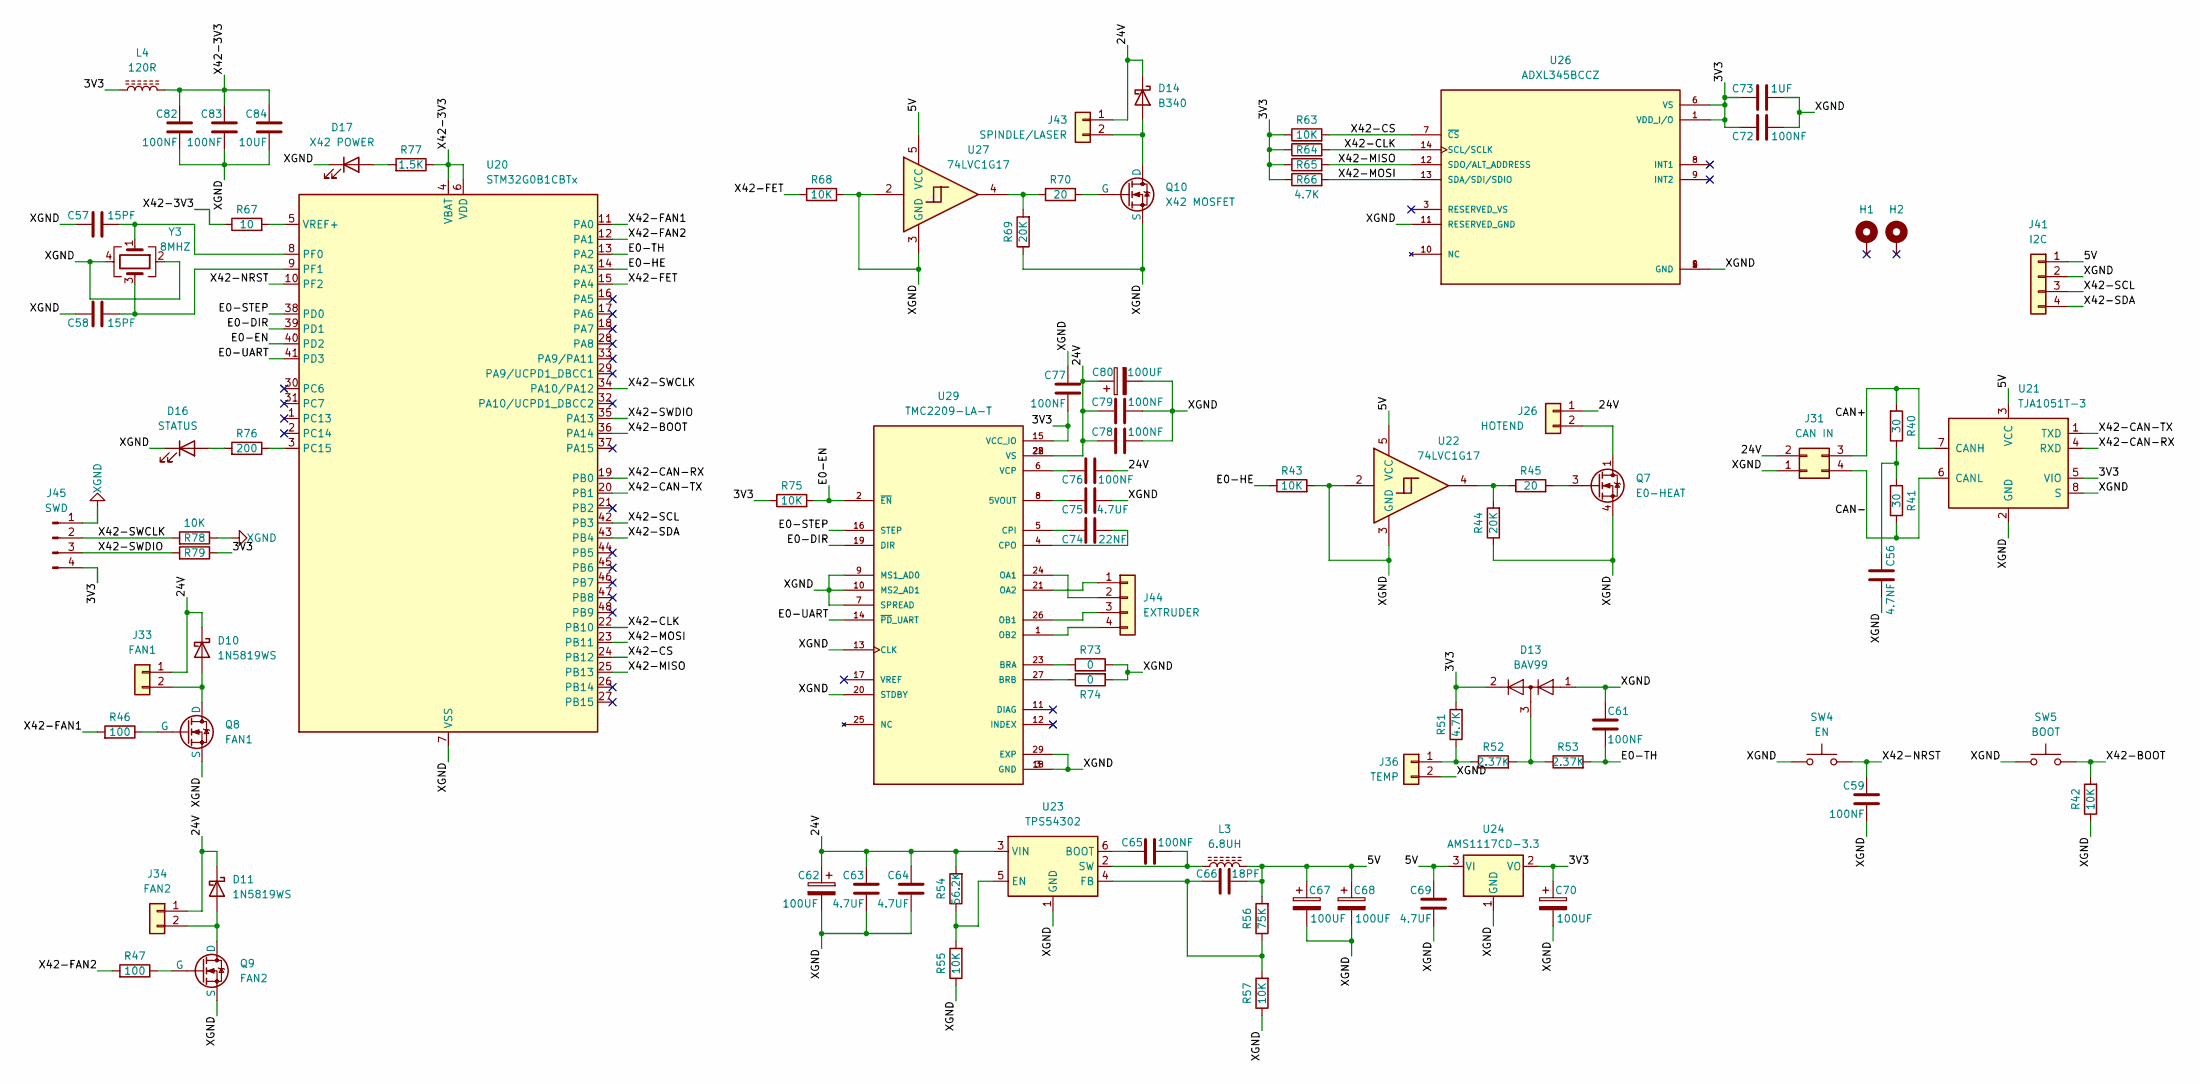
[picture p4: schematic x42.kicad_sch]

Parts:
C56: 4.7NF; C_0805_2012Metric
C57, C58: 15PF; C_0805_2012Metric
C59, C61, C65, C72, C76, C77, C78, C79, C82, C83: 100NF; C_0805_2012Metric
C62, C67, C68, C70, C80: 100UF; CP_Elec_5x3
C63, C64, C69, C75: 4.7UF; C_0805_2012Metric
C66: 18PF; C_0805_2012Metric
C73: 1UF; C_0805_2012Metric
C74: 22NF; C_0805_2012Metric
C84: 10UF; C_0805_2012Metric
D10, D11: 1N5819WS; D_SOD-323
D13: BAV99; SOT-23
D14: B340; D_SMC
D16: STATUS; LED_0805_2012Metric
D17: X42 POWER; LED_0805_2012Metric
H1, H2: MountingHole_Pad; MountingHole_3mm_Pad
J26: HOTEND; JST_XH_B2B-XH-A_1x02_P2.50mm_Vertical
J31: CAN IN; Molex_Micro-Fit_3.0_43045-0400_2x02_P3.00mm_Horizontal
J33: FAN1; PinHeader_1x02_P2.54mm_Vertical_SMD_Pin1Right
J34: FAN2; PinHeader_1x02_P2.54mm_Vertical_SMD_Pin1Right
J36: TEMP; JST_XH_B2B-XH-A_1x02_P2.50mm_Vertical
J41: I2C; PinHeader_1x04_P2.54mm_Vertical_SMD_Pin1Right
J43: SPINDLE/LASER; PinHeader_1x02_P2.54mm_Vertical_SMD_Pin1Right
J44: EXTRUDER; JST_XH_B4B-XH-A_1x04_P2.50mm_Vertical
J45: SWD; PinHeader_1x04_P2.54mm_Vertical_SMD_Pin1Right
L3: 6.8UH; L_6.3x6.3_H3
L4: 120R; L_0805_2012Metric
Q7: E0-HEAT; Vishay_PowerPAK_SC70-6L_Single
Q8: FAN1; SOT-23
Q9: FAN2; SOT-23
Q10: X42 MOSFET; TO-252-2
R40, R41: 30; R_0805_2012Metric
R42, R43, R55, R57, R63, R68, R75, R78, R79: 10K; R_0805_2012Metric
R44, R69: 20K; R_0805_2012Metric
R45, R70: 20; R_0805_2012Metric
R46, R47: 100; R_0805_2012Metric
R51, R64, R65, R66: 4.7K; R_0805_2012Metric
R52, R53: 2.37K; R_0805_2012Metric
R54: 56.2K; R_0805_2012Metric
R56: 75K; R_0805_2012Metric
R67: 10; R_0805_2012Metric
R73, R74: 0; R_0805_2012Metric
R76: 200; R_0805_2012Metric
R77: 1.5K; R_0805_2012Metric
SW4: EN; SW_Tactile_SPST_NO_Straight_CK_PTS636Sx25SMTRLFS
SW5: BOOT; SW_Tactile_SPST_NO_Straight_CK_PTS636Sx25SMTRLFS
U20: STM32G0B1CBTx; LQFP-48_7x7mm_P0.5mm
U21: TJA1051T-3; SOIC-8_3.9x4.9mm_P1.27mm
U22, U27: 74LVC1G17; SOT-23-5
U23: TPS54302; SOT-23-6
U24: AMS1117CD-3.3; TO-252-2
U26: ADXL345BCCZ; IC_ADXL345BCCZ; PARTREV G
U29: TMC2209-LA-T; QFN50P500X500X90-29N; PARTREV 1.09
Y3: 8MHZ; Crystal_SMD_Abracon_ABM3B-4Pin_5.0x3.2mm

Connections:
/X42/3V3: C70.1, C72.1, C73.1, C77.2, D13.2 (A), J45.4, L4.1, R51.2, R63.1, R64.1, R65.1, R66.1, R75.1, R79.1, U21.5 (VIO), U24.2 (VO), U26.1 (VDD_I/O), U26.6 (VS), U29.15 (VCC_IO)
/X42/5V: C66.1, C67.1, C68.1, C69.1, J41.1, L3.2, R56.2, U21.3 (VCC), U22.5 (VCC), U24.3 (VI), U27.5 (VCC)
/X42/24V: C62.1, C63.1, C64.1, C76.1, C78.2, C79.2, C80.1, D10.1 (K), D11.1 (K), D14.1 (K), J26.1, J31.2, J33.1, J34.1, J43.1, R54.2, U23.3 (VIN), U29.22 (VS), U29.28 (VS)
/X42/CAN+: J31.3, R40.2, U21.7 (CANH)
/X42/CAN-: J31.4, R41.1, U21.6 (CANL)
/X42/E0-DIR: U20.39 (PD1), U29.19 (DIR)
/X42/E0-EN: R75.2, U20.40 (PD2), U29.2 (~EN)
/X42/E0-HE: R43.1, U20.14 (PA3)
/X42/E0-STEP: U20.38 (PD0), U29.16 (STEP)
/X42/E0-TH: C61.2, R53.2, U20.13 (PA2)
/X42/E0-UART: U20.41 (PD3), U29.14 (~PD_UART)
/X42/X42-3V3: C82.1, C83.1, C84.1, L4.2, R67.1, R77.1, U20.4 (VBAT), U20.6 (VDD)
/X42/X42-BOOT: R42.2, SW5.2, U20.36 (PA14)
/X42/X42-CAN-RX: U20.19 (PB0), U21.4 (RXD)
/X42/X42-CAN-TX: U20.20 (PB1), U21.1 (TXD)
/X42/X42-CLK: R64.2, U20.22 (PB10), U26.14 (SCL/SCLK)
/X42/X42-CS: R63.2, U20.24 (PB12), U26.7 (~CS)
/X42/X42-FAN1: R46.2, U20.11 (PA0)
/X42/X42-FAN2: R47.2, U20.12 (PA1)
/X42/X42-FET: R68.1, U20.15 (PA4)
/X42/X42-MISO: R65.2, U20.25 (PB13), U26.12 (SDO/ALT_ADDRESS)
/X42/X42-MOSI: R66.2, U20.23 (PB11), U26.13 (SDA/SDI/SDIO)
/X42/X42-NRST: C59.1, SW4.2, U20.10 (PF2)
/X42/X42-SCL: J41.3, U20.42 (PB3)
/X42/X42-SDA: J41.4, U20.43 (PB4)
/X42/X42-SWCLK: J45.2, R78.2, U20.34 (PA10/PA12)
/X42/X42-SWDIO: J45.3, R79.2, U20.35 (PA13)
unnamed: C56.1, R40.1, R41.2
unnamed: D10.2 (A), J33.2, Q8.1 (D)
unnamed: D11.2 (A), J34.2, Q9.1 (D)
unnamed: D13.3 (K), R52.2, R53.1
unnamed: D14.2 (A), J43.2, Q10.1 (D)
unnamed: D16.2 (A), R76.2
unnamed: D17.2 (A), R77.2
unnamed: J26.2, Q7.1 (D)
unnamed: J36.1, R51.1, R52.1
unnamed: J44.1, U29.21 (OA2)
unnamed: J44.2, U29.24 (OA1)
unnamed: J44.3, U29.26 (OB1)
unnamed: J44.4, U29.1 (OB2)
unnamed: Q7.3 (G), R45.2
unnamed: Q8.2 (G), R46.1
unnamed: Q9.2 (G), R47.1
unnamed: Q10.2 (G), R70.2
unnamed: R44.2, R45.1, U22.4
unnamed: R69.2, R70.1, U27.4
unnamed: R76.1, U20.3 (PC15)
unnamed: C57.2, U20.8 (PF0), Y3.1
unnamed: C58.2, U20.9 (PF1), Y3.3
unnamed: R67.2, U20.5 (VREF+)
unnamed: C65.2, U23.6 (BOOT)
unnamed: R54.1, R55.2, U23.5 (EN)
unnamed: C66.2, R56.1, R57.2, U23.4 (FB)
unnamed: C65.1, L3.1, U23.2 (SW)
unnamed: C75.2, U29.8 (5VOUT)
unnamed: R73.1, U29.23 (BRA)
unnamed: R74.1, U29.27 (BRB)
unnamed: C74.2, U29.5 (CPI)
unnamed: C74.1, U29.4 (CPO)
unnamed: C76.2, U29.6 (VCP)
XGND: C56.2, C57.1, C58.1, C59.2, C61.1, C62.2, C63.2, C64.2, C67.2, C68.2, C69.2, C70.2, C72.2, C73.2, C75.1, C77.1, C78.1, C79.1, C80.2, C82.2, C83.2, C84.2, D13.1 (K), D16.1 (K), D17.1 (K), J31.1, J36.2, J41.2, J45.1, Q7.4 (S), Q8.3 (S), Q9.3 (S), Q10.3 (S), R42.1, R43.2, R44.1, R55.1, R57.1, R68.2, R69.1, R73.2, R74.2, R78.1, SW4.1, SW5.1, U20.7 (VSS), U21.2 (GND), U21.8 (S), U22.2, U22.3 (GND), U23.1 (GND), U24.1 (GND), U26.2 (GND), U26.4 (GND), U26.5 (GND), U26.11 (RESERVED_GND), U27.2, U27.3 (GND), U29.3 (GND), U29.7 (SPREAD), U29.9 (MS1_AD0), U29.10 (MS2_AD1), U29.13 (CLK), U29.18 (GND), U29.20 (STDBY), U29.29 (EXP), Y3.2, Y3.4

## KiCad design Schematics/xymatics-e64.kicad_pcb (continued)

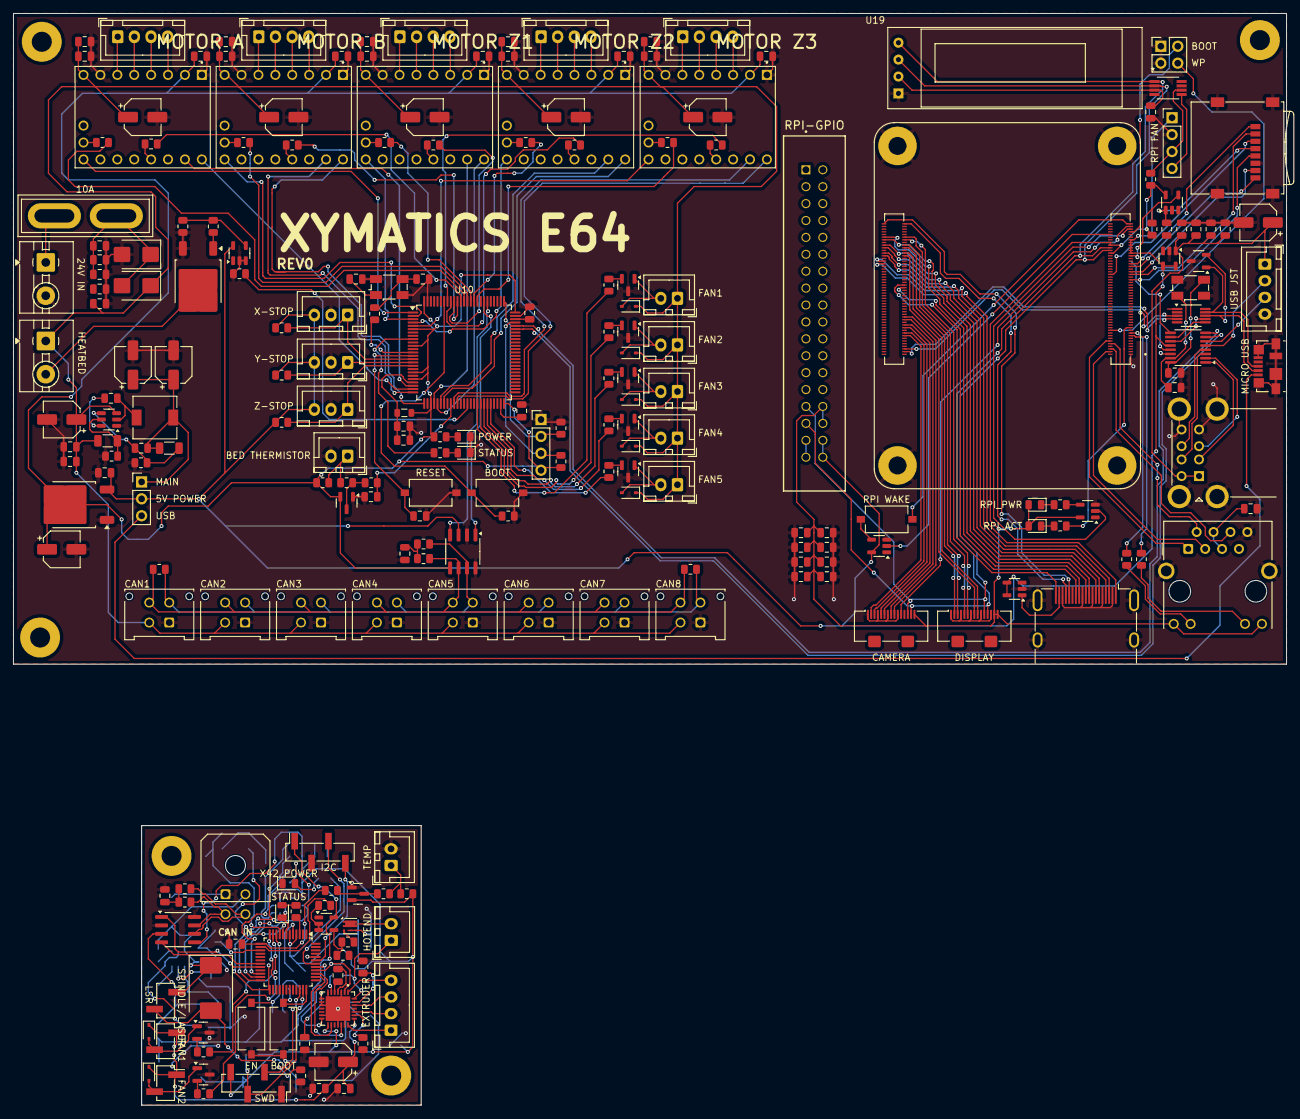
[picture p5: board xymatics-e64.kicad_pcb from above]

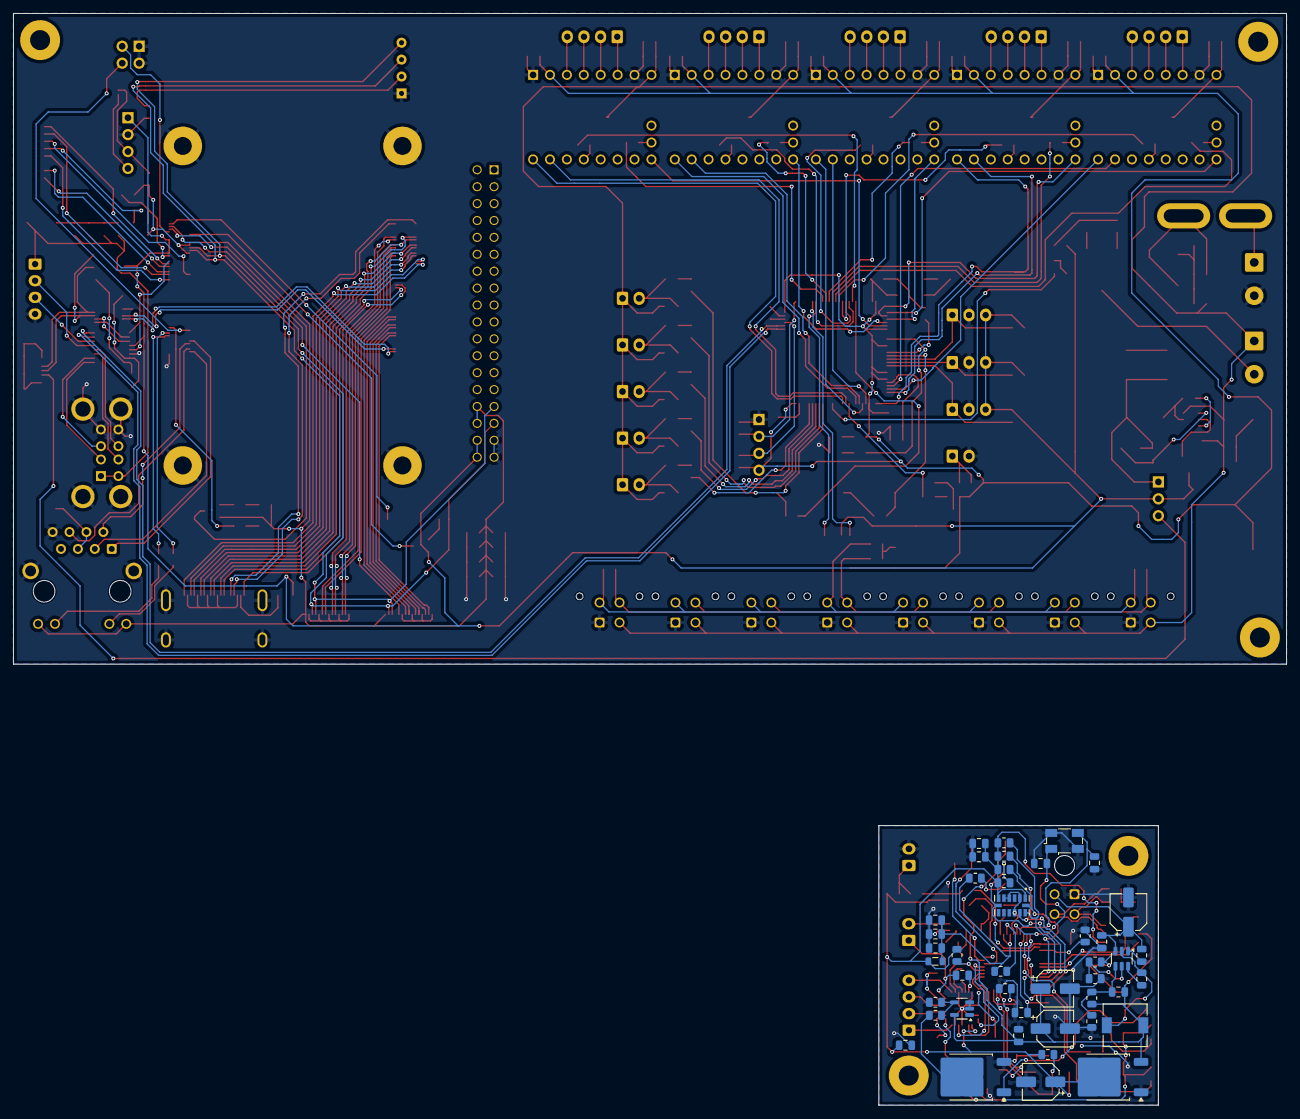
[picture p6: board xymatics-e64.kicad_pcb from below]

Board: 2 copper layers, 191.2 x 164.0 mm, 282 parts (43 on the bottom side), 275 nets.

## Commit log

2025-07-20 Create JOURNAL.md
    7/07/2025 - Begin PCB design
2025-07-20 Add xymatics-e64.kicad_sch
    [xymatics-e64.kicad_sch]
2025-07-20 Add cm4.kicad_sch
    [cm4.kicad_sch]
2025-07-20 Update JOURNAL.md
    # 14/07/2025 - Finish STM32 schematic and begin X42 schematic
2025-07-20 Add x42.kicad_sch
    [x42.kicad_sch]
2025-07-20 Update JOURNAL.md
    20/07/2025 - Finish X42 schematic
2025-07-20 Update Schematics
    Update CM4, X42, XYmatics-E64 schematics
    [cm4.kicad_sch, x42.kicad_sch, xymatics-e64.kicad_sch]
2025-07-23 Update X42 schematics, Add project PCB
    Removed Neopixel and BLTouch breakouts from X42, added X42 PCB (unfinished)
    [cm4.kicad_sch, x42.kicad_sch, xymatics-e64.kicad_pcb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]
2025-07-23 Update README.md
    Edit X42 Features, Add X42 PCB renders
2025-07-24 Update JOURNAL.md
    25/07/2025 - Finish X42 PCB
2025-07-24 Update X42 schematics, Update X42 PCB
    Removed X42 Endstops (re-add in next revision)
    [x42.kicad_sch, xymatics-e64.kicad_pcb]
2025-08-03 Update JOURNAL.md
    31/07/2025 - E64 PCB complete
2025-08-03 Update E64 schematics
    Finish E64 PCB
    [cm4.kicad_sch, x42.kicad_sch, xymatics-e64.kicad_pcb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]
2025-08-03 Add gerber files
    [xymatics-e64-B_Cu.gbr, xymatics-e64-B_Mask.gbr, xymatics-e64-B_Paste.gbr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]
2025-08-03 Update README.md
    Update PCB renders
